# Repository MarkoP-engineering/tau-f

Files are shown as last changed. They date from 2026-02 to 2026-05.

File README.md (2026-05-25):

This is a repository for the development of a model rocket for the Czech Rocket Challenge 2026 competition.

The rocket will have to ignite it`s engine, launch, climb up to 800 meters, release the parachute and return safely.

The fuselage will be 3D printed out of Prusament ASA due to it's low density and extreme durability. The whole body will weight about 650g
The bodz will be split into multiple sections - below they are in order form bottom to top
- Tail + fin module - a part that contains the stabilizing aerodynamic elements of the rocket and will help keep the rocket engine in place
- Engine + egg section - a large section the engine is screwed into from the bottom that also contains sace to put a chicken egg to be flown on the rocket
- Barometer section - a section for the mandate barometer to be mounted
- Avionics section - will contain most of the elctronics needed for the rocket to function - custom flight controller, camera, battery and a connector for external power while on standby
- Nosecone and ejection system - a system toggled electrically and powered by a spring for the release of the parachute to assure the safe return of the rocket

We would like to thank Prusa Research for providing us with the filament necessary to make this project possible!


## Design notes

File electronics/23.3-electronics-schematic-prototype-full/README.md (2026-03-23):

This is the first full schematic for the avionics of the rocket.
It contains:
- USB C port for data and power
- Voltage step down converter to 3.3V
- RP2040 microcontroller with components necessary for its function
- MPU6000 accelerometer and gyroscope module
- NEO-M8M GPS module
- MPL115A1 digital barometer module
- E22-400MM22S LoRa 400 Mhz radio transmitter module
All of the modules communicate with the microcontroller via an SPI bus
This is a very rough prototype, and I probably made a lot of mistakes. Everything will most likely be remade from scratch according to the documentationand double-checked.
I had to create a custom symbol for the LoRa module. All of the custom symbols, and later footprints, will be placed into their respective update folders.

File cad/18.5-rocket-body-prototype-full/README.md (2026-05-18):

This is the first full prototype of the rocket prototype. The model was completely rebuilt as an assembly with each module being its own component,
Changes:
- Adjusted fin size and shape
- Designed the final motor mount
- Redesigned the carbon rod mountings to leae more internal space
- Added the holder for the barometer
- Added a protottype for the connector between modules - holds 20kg but most likely can be optimised further

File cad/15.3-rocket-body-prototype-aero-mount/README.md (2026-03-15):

Another prototype of the rocket fuselage with minimal changes.
Changes:
- Redesigned the fins to print as one piece with the engine mount, reducing complexity and increasing rigidity
- Added a crude prototype of the enginee mount - sizes of the screw hole and friction mount TBD

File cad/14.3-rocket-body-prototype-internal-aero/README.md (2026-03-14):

This is the second prototype of the model rocket body. 
Changes:
- Added internal cavities for the avionics, egg, and altimeter sections
- Added stabilizers
The stabilizers are currently mounted via a dovetail connection. Untested so far, will print and test later.

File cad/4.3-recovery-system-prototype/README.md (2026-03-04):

This is my first prototype of the recovery system, that is supposed to eject the parachute.
The energy is stored in a spring. We settled on this approach for its relative simplicity and reliability. Additionally, ejection charges are really hard to oobtain and CO2 cartridges are non reusable.
This design utilizes a servo to rotate the whole nosecone via a system of gears similar to a clutch in an automobile. After the nosecone is rotated, kts pins are free which releases the tension from the spring.
The parachute will be connected to the middle part via a velcro. The nosecone will be ejected on a piece of rope, pulling the parachute out afterwards. This is to ensure the parachute does not stay inside the nosecone after deployemnt.
NOTE TO SELF - ADD RIDGE FOR MIDDLE PART TO STAY IN PLACE
The 3 bodies are: 
- Nosecone and upper "clutch" part
- Middle gear part that will be attached to the servo head (further adjustments are needed as I havent yet had the time to print the frdign)
- Bottom fuselage part - the servo is mounted here
Next I intend to test the design and create modifiers for better printing and durabiliy.

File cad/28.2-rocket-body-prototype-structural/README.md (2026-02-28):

This is the first prototype of the rocket body designed with actual flight in mind. Features internal bracing and spaces for 2.5mm carbon rods to bhe inserted into. 
I modeled in the rough openings for the barometers and the camera (?)
This is meant to be used mostly for simulations to mimic the weight distribution and aerodynamic propeerties of the final rocket.
Uploaded on 28.2.2026

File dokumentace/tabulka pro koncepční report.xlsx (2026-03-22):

Kategorie | SŠ začátečníci
Předpokládané apogeum (m) | 411
Předpokládaná délka (mm) | 860
Průměr trupu (mm | 60
Očekávaná hmotnost (g) | 1235/1613(bude se snižovat vylepšením vnitřní struktury)
Stabilita při opuštění rampy (cal.) | 2,08
Stabilita maximální (v cal.) | 3,32
Doba letu (s) | 50,4
Maximální akcelerace (m · s−2) | 79,6

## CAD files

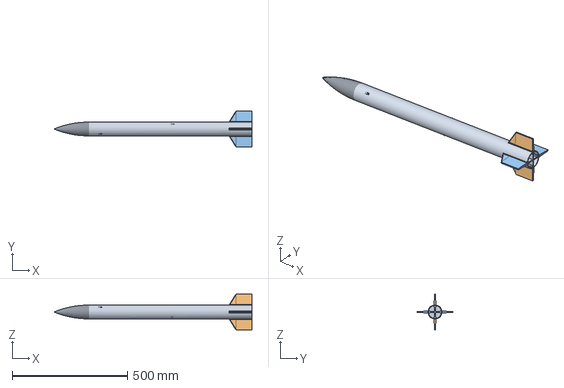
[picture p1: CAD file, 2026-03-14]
cad/14.3-rocket-body-prototype-internal-aero/14.3-rocket-body-prototype-structural-aero.step
860.0 x 155.0 x 155.0 mm

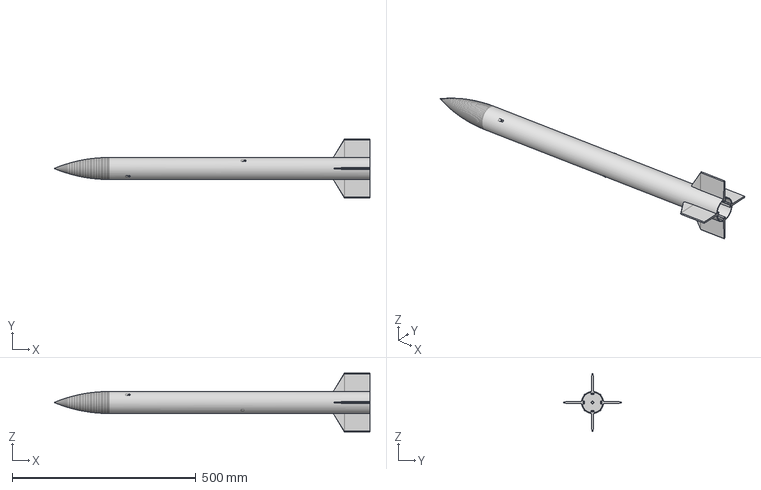
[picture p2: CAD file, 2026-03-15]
cad/15.3-rocket-body-prototype-aero-mount/15.3-rocket-body-prototype-aero-mount.step
860.0 x 160.0 x 160.0 mm

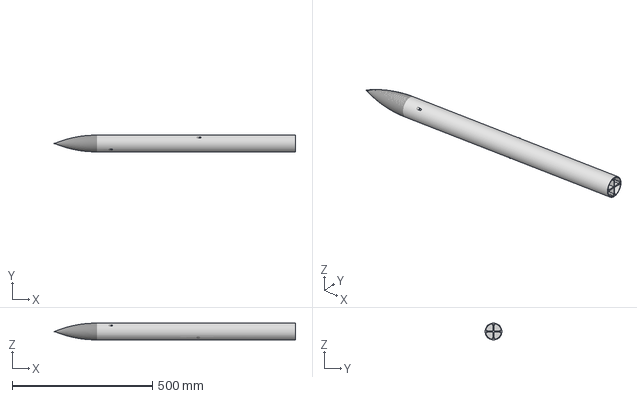
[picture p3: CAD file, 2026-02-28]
cad/28.2-rocket-body-prototype-structural/28.2-body-prototype-structural.step
860.0 x 60.0 x 59.9 mm

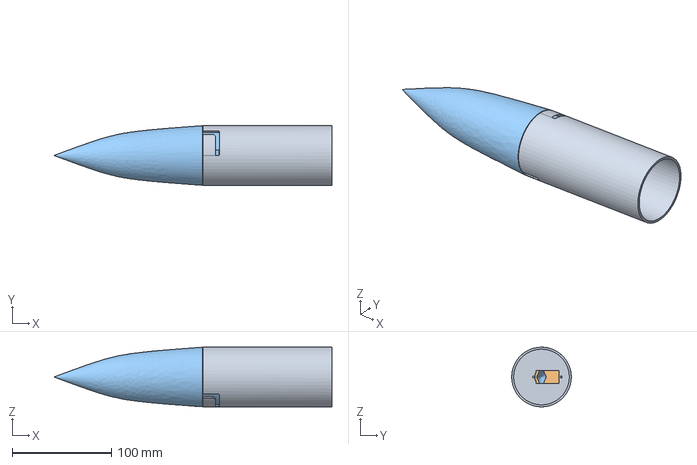
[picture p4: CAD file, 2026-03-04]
cad/4.3-recovery-system-prototype/4.3-recovery-system-prototype.step
279.5 x 60.0 x 60.0 mm

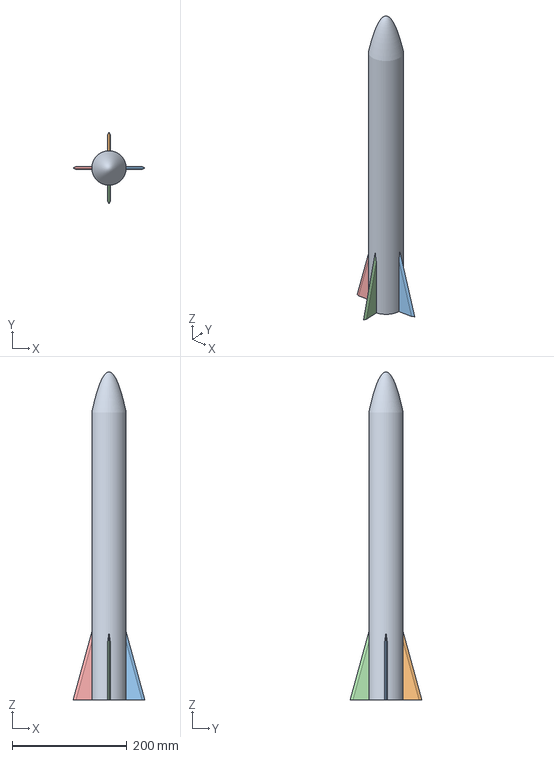
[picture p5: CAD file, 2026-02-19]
cad/Part Studio 1 - Composite part 1 (1).3mf
125.0 x 125.0 x 570.5 mm

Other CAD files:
cad/18.5-rocket-body-prototype-full/raketa_18.5.26_20_46.f3z

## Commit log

2026-02-19 prvotní návrh aerodinamických prvků rakety
    vše je naprosto od oka nic jsem nepočítal chci to zkusit popřípadě vylepšit spíš jsem si zkoušel cad
    [Part Studio 1 - Composite part 1 (1).3mf]
2026-02-28 Added STEP file with the rocket body and the necessary modifiers for 3d printing
    [28.2-body-prototype-structural.step]
2026-03-04 Added the .step files for the recovery system prototype
    [4.3-recovery-system-prototype.step]
2026-03-22 tabulka + ůprava prototypu
    [tabulka pro koncepční report.xlsx]
2026-03-23 Create README.md for the first full avionics schematic
2026-03-23 Added the schematic and custom symbol library file for the avionics
    [23.3-electronics-schematic-prototype-full.kicad_sch]
